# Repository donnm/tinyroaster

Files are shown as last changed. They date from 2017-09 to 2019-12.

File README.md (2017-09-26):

# tinyroaster

Arduino sketch for ATtiny85 or similar to be used in a coffee roasting controller board.

The design uses an ATtiny85 (see sketch for pinouts), MAX6675 temperature amplifier and type K thermocouple, 74HC165 shift register for interfacing with a Hitatchi compatible LCD in 4-bit mode.

The controller board manages timing, heater (via relay) and fan speed (~20V PWM) of a modified hot-air popcorn maker to roast small quantities of beans (40-100g).

## Operation

When the tinyroaster is powered on (SW1), the user is presented with three modes: Manual, Temperature, Profile. Manual mode lets the user control the fan speed with the pot and the heater with the heater override switch (SW2).

In Temperature mode, the user first chooses the fan speed (70, 80, 90 or 100% duty cycle), and then controls the temperature with the pot (range is set from 0-280C).

In Profile mode, the user can choose from one of the pre-programmed profiles. Currently those are Light, City, City+, Vienna, French. The roast then begins and progresses until the end, at which point the beans are cooled to around 50C and the roast is stopped.

### Emergency cool-down mode
If a roast fails or stops prematurely, leaving the beans in the hot chamber can be dangerous. An emergency mode is therefor accessible by turning the pot all the way to the right and resetting the tinyroaster with the power switch (SW1). In this mode the fan is at 100% duty cycle and the heater is disabled, quickly cooling the chamber.

## Hot-air popper modifications

In order to control the heater and fan independently, the fan must be decoupled from the heater. How you do this depends on the brand/model. There are lots of resources online already for how to do this, such as http://www.instructables.com/id/Build-a-Controllable-Coffee-Roaster-from-an-Air-Po/ and https://ineedcoffee.com/poplite-coffee-roaster/

## Schematic and parts list

The parts were mostly what I had lying around, which explains why some bizarre design decisions were made.

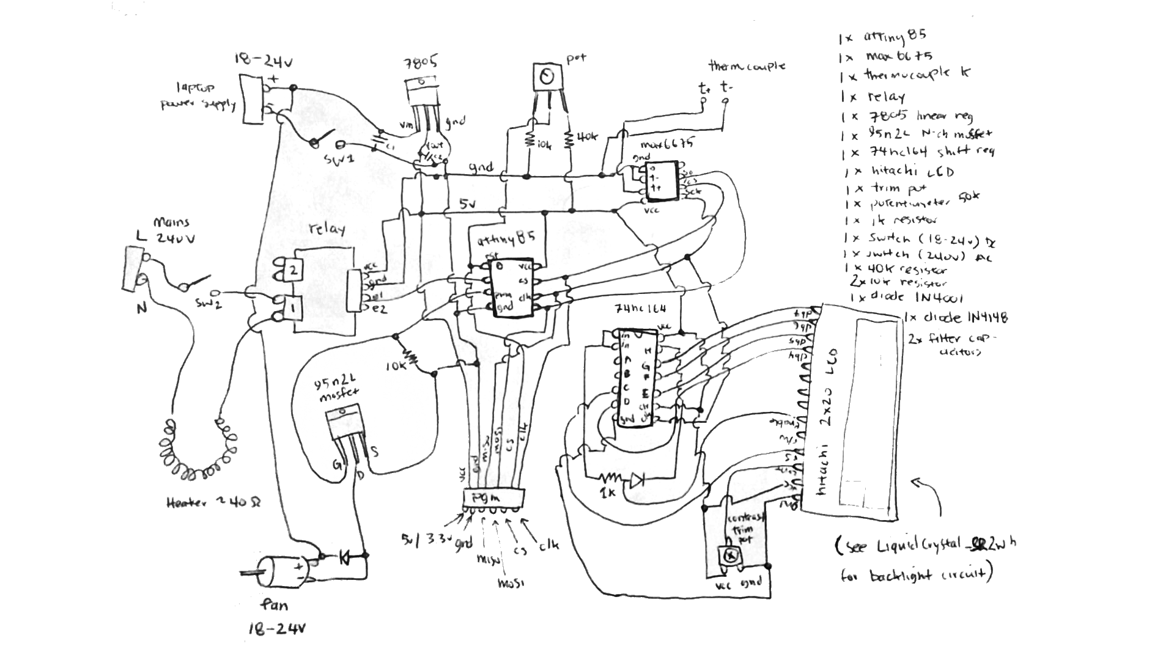
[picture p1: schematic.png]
Schematic and parts list


## Programming

A programmer header dangles out of the case so that I can connect a Bus Pirate and flash new software and roasting profiles using the Arduino IDE.

## Notes
### I/O pins
The ATtiny85 only has 5 I/O pins available, 6 if you can hold reset (pin 1) high enough while doing something useful with it. The 40k and 10k resistors do this, and allow us to read the potentiometer connected to this pin. This pot is the only user input, so it controls the fan speed, temperature, menu system, depending on what mode we're in.

The LCD uses a 74HC164 shift register, which needs 2 pins (data, clock). The MAX6675 thermocouple IC needs three pins (/cs, clock, data). Heater relay one pin, fan PWM one pin. To get around the shortage I share pins between the shift register and MAX6675. This mostly works well, with some caveats. The LCD update code in the Arduino sketch needs a few hacks to make it run without corruption. I arrived at this mostly by trial and error. This could all be easily solved by using an Arduino compatible microcontroller with more I/O pins.

### RFI issues
Combining mains electricity, ~20V DC PWM and a poorly organised mess of wires inside a box is a recipe for radio frequency interference. Early versions had issues with LCD corruption and random ATtiny resets, but these appear to be solved by the installation of ferrite beads on data lines, on the fan PWM, and better organising and separating bunches of wires. I'm no expert on the subject so if you happen to spot other potential sources please let me know.

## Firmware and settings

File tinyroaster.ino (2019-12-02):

#include <avr/pgmspace.h>
#include <SendOnlySoftwareSerial.h>
#include <max6675.h>
#include <EEPROM.h>
#include <LiquidCrystal_SR2W.h>

/* Wiring
                  attiny85
                    +----+
(a0/rst/pot/pgm-cs)-|1  8|-(vcc)
  (heater relay/d3)-|2  7|-(d2/therm cs+lcd data/en/pgm-clk)
       (fan pwm/d4)-|3  6|-(d1/serial tx/therm+sr clocks/pgm-miso)
              (gnd)-|4  5|-(d0/therm do/pgm-mosi)
                    +----+

      max6675K
       +----+
 (gnd)-|1  8|-(nc)
  (t-)-|2  7|-(so)
  (t+)-|3  6|-(/cs)   pull /cs to vcc
 (vcc)-|4  5|-(sck)
       +----+

NOTES:
- Seems to require this verison of attiny to build:
  https://raw.githubusercontent.com/damellis/attiny/ide-1.6.x-boards-manager/package_damellis_attiny_index.json

TODO:
- bug - getRelativeInput countdown strangeness
- bug - linearise pot readings
- feature - PID control for heater
*/

#define RXPIN 0
#define TXPIN 1
#define PWMPIN 4
#define HEATERPIN 3
#define THERMCS 2
#define SRDATAEN 2
#define THERMCLK 1
#define SRCLK 1
#define THERMDO 0
#define POTPIN A0
#define POTMIN 528
#define POTMAX 956
#define MINFANHEAT 4
#define POTSENSITIVITY 5
#define BANNERMS 1000
#define LCD_ROWS 2
#define LCD_COLS 20
#define MAXTEMP 280

#define ROASTMANUAL 0
#define ROASTTEMP 1
#define ROASTPROFILE 2

const int lastRoastValidAddr = 0;
const int lastRoastProfileAddr = 1;

bool started = false;
bool emergency = false;
unsigned long curr_time = 0;
unsigned long stopped_time = 0;
unsigned long startup_time = 0;
short numzeros = 0; // Error tracking for temp sensor
short stage = 0;
short num_stages = 0;
double target_temp = 0.0;
double lastpot;
byte roastmode = ROASTMANUAL;
byte roastprofile = 0;
double roast_temp_fan_speed = 0.8;
//short *stages_secs;
short *stages_temp;

/* String table
 *  Use PROGMEM to store in flash
 */
const char str_you_chose[] PROGMEM = "You chose ";

const char profile_light[]  PROGMEM = "Light";
const char profile_city[]   PROGMEM = "City";
const char profile_cityp[]  PROGMEM = "City+";
const char profile_vienna[] PROGMEM = "Vienna";
const char profile_french[] PROGMEM = "French";

const char mode_manual[]  PROGMEM = "Manual";
const char mode_temp[]    PROGMEM = "Temperature";
const char mode_profile[] PROGMEM = "Profile";

const char fanspeed_70[]  PROGMEM = "70%";
const char fanspeed_80[]  PROGMEM = "80%";
const char fanspeed_90[]  PROGMEM = "90%";
const char fanspeed_100[] PROGMEM = "100%";

const char* const profile_choices[]  PROGMEM = {profile_light, profile_city, profile_cityp, profile_vienna, profile_french};
const char* const mode_choices[]     PROGMEM = {mode_manual, mode_temp, mode_profile};
const char* const fanspeed_choices[] PROGMEM = {fanspeed_70,fanspeed_80,fanspeed_90,fanspeed_100};

LiquidCrystal_SR2W lcd(SRDATAEN,SRCLK, NEGATIVE);
MAX6675 thermocouple(THERMCLK, THERMCS, THERMDO);
SendOnlySoftwareSerial Serial(TXPIN); //tx

void mainMenu();
void profileMenu();
void tempMenu();
void doRoast();
bool loadProfile();
bool saveProfile();
int getRelativeInput(const char* prompt, double timeoutms, bool wrap, bool allownone, int numchoices, const char** choices);

/* Roast profiles
 *  Since these are all 10 minute profiles, and the timings are the same, only
 *  use one array for timings (stage_secs). May adjust later as needed. Saves RAM.
 *  
 *  Number of stages calculated based on the number of non-zero entries in
 *  *_stages_temp. 0-terminated integer array.
 */
short stages_secs[]           = {0,   160, 220, 280, 340, 380, 420, 480, 520};

short light_stages_temp[]     = {185, 190, 195, 200, 205, 0,   0,   0,   0};
short city_stages_temp[]      = {200, 204, 205, 206, 208, 0,   0,   0,   0};
short citypluss_stages_temp[] = {200, 208, 212, 216, 220, 225, 0,   0,   0};
short vienna_stages_temp[]    = {200, 210, 215, 220, 225, 230, 235, 0,   0};
short french_stages_temp[]    = {200, 210, 215, 220, 227, 235, 240, 245, 0};

void setup()
{
  pinMode(HEATERPIN, OUTPUT);
  digitalWrite(HEATERPIN, LOW);

  lcd.begin(LCD_COLS,LCD_ROWS);

  Serial.begin(9600);
  Serial.println("BOOT");

  // Special startup modes: {emergency: pot far right, last roast profile: pot far left}
  lastpot = analogRead(POTPIN);
  int recallvalid = EEPROM.read(lastRoastValidAddr);
  int recallprof = EEPROM.read(lastRoastProfileAddr);
  if(lastpot >= POTMAX - 10)
  {
    // Emergency fan mode - heat off, cool down beans ASAP
    roastmode = ROASTMANUAL;
    started = true;
    emergency = true;
  }
  else if(lastpot <= (POTMIN + 10) && recallvalid && recallprof >= 0 && recallprof <= 4)
  {
    // Select last saved roast mode (profile only)
    roastmode = ROASTPROFILE;
    roastprofile = recallprof;
    switch(roastprofile+1)
    {
      case 1:
        stages_temp = light_stages_temp;
        break;
      case 2:
        stages_temp = city_stages_temp;
        break;
      case 3:
        stages_temp = citypluss_stages_temp;
        break;
      case 4:
        stages_temp = vienna_stages_temp;
        break;
      case 5:
        stages_temp = french_stages_temp;
        break;
    }
    started = true;
    lcd.clear();
    lcd.setCursor(0,0);
    lcd.print(F("Recalling profile:"));
    lcd.setCursor(0,1);
    char buff[LCD_COLS+1];
    strcpy_P(buff, (char*)pgm_read_word(&(profile_choices[roastprofile])));
    lcd.print(buff);
    delay(1000);
  }
  else
  {
    // Normal mode
    lcd.clear();
    lcd.setCursor(20,0);
    if(emergency)
      lcd.print(F("*Emergency *"));
    else
      lcd.print(F("*   Tiny   *"));
    lcd.setCursor(20,1);
    if(emergency)
      lcd.print(F("*   Mode   *"));
    else
      lcd.print(F("* Roaster  *"));
    for (int i=0; i<16; i++)
    {
      lcd.scrollDisplayLeft();
      delay(75);
    }
    delay(BANNERMS);
  
    delay(500);
  }
}

void loop()
{
  if(!started)
  {
    mainMenu();
    lcd.clear();
  
    switch(roastmode)
    {
      case ROASTPROFILE:
        profileMenu();
        break;
      case ROASTTEMP:
        tempMenu();
        break;
      case ROASTMANUAL:
        break;
    }

    lcd.clear();

    started = true;
    startup_time = millis();
    Serial.println("BEGIN");
  }

  while(true) doRoast();
}

void mainMenu()
{
  int pos = getRelativeInput(PSTR("Select mode: "),
    10000,
    false,
    false,
    3,
    mode_choices);
  lcd.clear();
  lcd.setCursor(0,0);
  char buff[LCD_COLS+1];
  strcpy_P(buff, str_you_chose);
  lcd.print(buff);
  strcpy_P(buff, (char*)pgm_read_word(&(mode_choices[pos-1])));
  lcd.print(buff);
  switch(pos)
  {
    case 1:
      roastmode = ROASTMANUAL;
      break;
    case 2:
      roastmode = ROASTTEMP;
      break;
    case 3:
      roastmode = ROASTPROFILE;
      break;
  }
  delay(1000);
}

void profileMenu()
{
  int pos = getRelativeInput(PSTR("Select profile: "),
    10000,
    false,
    false,
    5,
    profile_choices);
  lcd.clear();
  lcd.setCursor(0,0);
  char buff[LCD_COLS+1];
  strcpy_P(buff, str_you_chose);
  lcd.print(buff);
  strcpy_P(buff, (char*)pgm_read_word(&(profile_choices[pos-1])));
  roastprofile = pos-1;
  lcd.print(buff);
  switch(pos)
  {
    case 1:
      stages_temp = light_stages_temp;
      break;
    case 2:
      stages_temp = city_stages_temp;
      break;
    case 3:
      stages_temp = citypluss_stages_temp;
      break;
    case 4:
      stages_temp = vienna_stages_temp;
      break;
    case 5:
      stages_temp = french_stages_temp;
      break;
  }
  roastprofile = pos-1;
  EEPROM.write(lastRoastValidAddr, true);
  EEPROM.write(lastRoastProfileAddr, roastprofile);
  delay(1000);
}

void tempMenu()
{
  int pos = getRelativeInput(PSTR("Select fan speed: "),
    10000,
    false,
    false,
    4,
    fanspeed_choices);
  lcd.clear();
  lcd.setCursor(0,0);
  char buff[LCD_COLS+1];
  strcpy_P(buff, str_you_chose);
  lcd.print(buff);
  strcpy_P(buff, (char*)pgm_read_word(&(fanspeed_choices[pos-1])));
  lcd.print(buff);
  switch(pos)
  {
    case 1:
      roast_temp_fan_speed = 0.7;
      break;
    case 2:
      roast_temp_fan_speed = 0.8;
      break;
    case 3:
      roast_temp_fan_speed = 0.9;
      break;
    case 4:
      roast_temp_fan_speed = 1;
      break;
  }
  delay(1000);
}

void doRoast()
{
  // heat (true/false), fanpwm (0-255)
  // These are set in the loop body and only acted on
  // at the end of the routine.
  bool heat = false;
  double fanpwm = 0;
  char lcdbuff[LCD_COLS];
  double potreading = 0.0;
  double tempreading = 0.0;

  curr_time = (millis()-startup_time)/1000.0;
  /* stopped_time: save the time we finished so we can display it 
   * statically while keeping time timer going so we can flash between
   * roastmode and roastprofile for nicer UI
   */
  if(started)
    stopped_time = curr_time;

  // Multiple temperature readings to reduce noise
  int temps[10];
  for(int i=0; i<10; i++)
  {
    // Thermo reading
    digitalWrite(THERMCS,HIGH);
    delay(5);
    temps[i] = thermocouple.readCelsius();
    digitalWrite(THERMCS, LOW);
    delay(5);
  }
  // Insertion sort on the array of readings
  for(int i=0; i<10; i++)
  {
    int j = i, t;
    while (j > 0 && temps[j] < temps[j-1])
    {
        t = temps[j];
        temps[j] = temps[j-1];
        temps[j-1] = t;
        j--;
    }
  }
  // Take median temperature
  tempreading = temps[7];

  Serial.println(tempreading);

  // Record failed readings
  if(tempreading == 0.0)
    numzeros++;
  
  // Pot reading
  potreading += analogRead(POTPIN);
  float val = (float)(potreading-POTMIN)/(float)(POTMAX-POTMIN);
  if(val < 0) val = 0; // || curr_time < 1.0
  if(val > 1.0) val = 1.0;

  // Mode-specific heat and fan control
  if(started)
  switch(roastmode)
  {
    case ROASTPROFILE:
      // Calculate number of stages if profile
      num_stages = 0;
      while(stages_temp[num_stages] != 0)
        num_stages++;
      // Include trailing zero
      num_stages++;
    
      // Which stage are we at?
      stage = 0;
      while(stage < num_stages && curr_time >= stages_secs[stage])
        stage++;
      target_temp = stages_temp[stage-1];

      // Heater control
      if(tempreading < target_temp + 2 && tempreading != 0) // zero temp reading can mean short in probe
        heat = true;
      // Fan control
      fanpwm = val*255;

      // Turn off fan if heat is off AND we're at last stage AND temp less than 50
      if(stage == num_stages && heat == false && tempreading < 50 && tempreading != 0.0)
      {
        fanpwm = 0;
        started = false;
      }
      break;
    case ROASTMANUAL:
      // Heater control
      if(val*9 >= MINFANHEAT && !emergency)
        heat = true;
      // Fan control
      fanpwm = val*255;
      break;
    case ROASTTEMP:
      target_temp = val*MAXTEMP;
      // Heater control
      if(tempreading < target_temp + 2 && tempreading != 0) // zero temp reading can mean short in probe
        heat = true;
      // Fan control
      fanpwm = roast_temp_fan_speed*255;
      break;
  }

  // Re-init LCD (avoids garbage chars due to shared pins with thermocouple)
  lcd.begin(LCD_COLS,LCD_ROWS);
  lcd.clear();

  // Display heat/fan status
  lcd.setCursor(0,0);
  lcd.print(heat?"H":"h");
  lcd.setCursor(0,1);
  lcd.print((int)((fanpwm/255)*9));

  // Display roast mode (and profile)
  lcd.setCursor(2,0);
  strcpy_P(lcdbuff, (char*)pgm_read_word(&(mode_choices[roastmode])));
  if(roastmode == ROASTPROFILE)
    if(curr_time % 4 == 0) // Alternate Mode + profile
      strcpy_P(lcdbuff, (char*)pgm_read_word(&(profile_choices[roastprofile])));
  // Truncate the string
  if(strlen(lcdbuff) > 8)
  {
    lcdbuff[7] = '.';
    lcdbuff[8] = '\0';
  }
  lcd.print(lcdbuff);

  // Display temperature and target
  lcd.setCursor(10,0);
  lcd.print((int)tempreading,1);
  lcd.print("C");
  if(roastmode != ROASTMANUAL)
  {
    lcd.setCursor(14,0);
    lcd.print(" (");
    lcd.print((int)target_temp,1);
    lcd.print(")");
  }

  // Display profile stage
  if(roastmode == ROASTPROFILE)
  {
    lcd.setCursor(2,1);
    if(!started)
    {
      // Show status of zero temperature reads
      if(curr_time % 4 == 0)
      {
        lcd.print(F("# 0C: "));
        lcd.print(numzeros);
      }
      else
      {
        lcd.print(F("Done!"));
        Serial.println("DONE");
      }
    }
    else
    {
      lcd.print(F("Stage "));
      lcd.print(stage);
      lcd.print(F("/"));
      lcd.print(num_stages);
    }
  }

  // If necessary, show we're in emergency cool-down mode
  if(roastmode == ROASTMANUAL && emergency)
  {
    lcd.setCursor(2,1);
    if(curr_time % 4 == 0)
      lcd.print(F("Heater off"));
    else
      lcd.print(F("Emerg. mode"));
  }

  // Display current time
  lcd.setCursor(15,1);
  lcd.print(stopped_time);
  lcd.print(" s");
  
  // Heat and fan control
  digitalWrite(HEATERPIN, heat?HIGH:LOW);
  analogWrite(PWMPIN, fanpwm);

  // Set thermocouple CS high after LCD activity (required!)
  digitalWrite(THERMCS,HIGH);

  // Long delay to make LCD more readable (less blinking)
  delay(250);

  // This required for stable LCD
  lcd.clear();
}

int getRelativeInput(const char* prompt, double timeoutms, bool wrap, bool allownone, int numchoices, const char** choices)
{
  int res = 0;
  double remainingms = timeoutms;
  double selectedms = 0;
  lastpot = analogRead(A0);
  char buff[LCD_COLS+1];

  while(remainingms > 0)
  {
    // Display menu prompt
    lcd.clear();
    lcd.setCursor(0,0);
    strncpy_P(buff, prompt, LCD_COLS);
    lcd.print(buff);

    char *ptr = buff;
    int cursorloc = 0;
    int remaining = LCD_COLS - 3;
    int startpos = res==0?0:res-1;
    for(int i=startpos; i<numchoices && remaining > 0; i++)
    {
      int len = strlen_P((char*)pgm_read_word(&(choices[i])));
      strncpy_P(ptr, (char*)pgm_read_word(&(choices[i])), remaining);
      if(res - 1 == i)
        cursorloc = ptr - buff;
      if(i != numchoices -1)
      {
        strcat(ptr++, " ");
        remaining--;
      }
      ptr += len;
      remaining -= len;
    }

    lcd.setCursor(0,1);
    lcd.print(buff);

    lcd.setCursor(18,1);
    lcd.print((int)(remainingms/1000.0));

    if(res > 0)
    {
      // Highlight selected menu item
      lcd.cursor();
      lcd.setCursor(cursorloc,1);
    }
    
    double pot = analogRead(A0);

    // Move selector to the left
    if(pot < lastpot - POTSENSITIVITY)
    {
      if(res > (allownone?0:1))
        res--;
      else if(wrap)
        // Wrap back to right!
        res = numchoices;

      if(res != 0)
      {
        selectedms = millis();
        remainingms = timeoutms;
      }
    }
    // Move selector to the right
    else if (pot > lastpot + POTSENSITIVITY)
    {
      if(res < numchoices)
        res++;
      else if(wrap)
        // Wrap back to left!
        res = 1;

      if(res != 0)
      {
        selectedms = millis();
        remainingms = timeoutms;
      }
    }
    
    remainingms = remainingms - (millis() - selectedms);
    
    // In non-choice position (nothing selected), disable timer
    if(res == 0)
    {
      selectedms = 0;
      remainingms = timeoutms;
    }

    lastpot = pot;
    delay(100);
  }

  lcd.noCursor();
  return res;
}

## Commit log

2017-08-21 integrated PID
2017-09-18 fritzing in progress
    [roaster.fzz]
2017-09-21 Cleanup of doRoast() Moved strings to flash strings table Rewrite of getRelativeInput() for more flexible menus Startup banner changed Updated .ino filename for compat with Arduino IDE Added option t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
    [tinyroaster.fzz]
2017-09-23 Adjusted vienna/french profiles (too hot for too long) Delay adjusted between therm CS high/low for spiread
    [tinyroaster.ino]
2017-09-24 Median filter temp readings Added emergency cool-down mode (start up with pot at max)
2017-09-26 Added schematic sketch
